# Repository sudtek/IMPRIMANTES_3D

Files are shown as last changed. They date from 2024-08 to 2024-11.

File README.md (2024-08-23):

# IMPRIMANTES_3D

24 août 2024

Ce repository dédié aux imprimantes 3D va regrouper mes howto et tutoriels principalement liés à certaines imprimantes 3D que j'utilise / posséde.
J'utilise principalement des imprimantes 3D pour l'impression de prototypes réalisée sous Catia V5 ,malheureusement par defaut les imprimantes 3D ne sont pas correctement calibrés par les constructeurs.
C'est donc à l'utilisateur de regler son imprimante via des étapes de calibrages pour esperer obtenir une objet 3D précis et fidéles au STL.

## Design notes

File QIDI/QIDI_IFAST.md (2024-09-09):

**24_08_2024**

J'ai recement fait l'acquisition d'une imprimante de marque QIDI modéle IFAST avec une tête dual pour pouvoir imprimer mes piéces du PETG et les supports dans une matiere differente (PLA / PVA) qui n'hadére pas au PETG.
 
 Une imprimante dite "dual" est différent d'une "IDEX" qui posséde deux têtes totalement indépandantes, capables de travailler simultanément, en mirroir en clone...

Les deux extrudeurs de la QIDI IFAST sont montés sur une unique tête et sont alternativement sortis / retractés selon le besoin via une came lorsque la tête arrive en buté gauche / droite. 

Exemple : Si la tête arrive en buté gauche la tête Z2 situé à main gauche est abaissée à proximité du plateau afin de pouvoir imprimmer alors que la tête de droite z1 est elle est retactée.

J'utilise uniquement le sclicer Ideamaker pour convertir mes fichiers STL. Celui-ci identifie les têtes de gauche à droite comme T0,T1 ... ce qui n'est pas sans posser des pb avec la numerotation de QUIDI.

**QUIDI IFAST avec Firmware Marlin modifié par QIDI; certaines fonctions gcodes sont diferentes voir la section [Firmware de la QUIDI IFAST ](https://github.com/sudtek/IMPRIMANTES_3D/tree/235f8ea74b5f1439434741d732e151d05a6209f9/QIDI/IFAST/Firmware)**

| Localisation Extrudeur | Gauche | Droite |
|---|---|---|
| Identification QIDI | Z2 | Z1 |
| Identification Ideamaker| T0 | T1 |
| Localisation | Gauche | Droite |
| Impression | Corps  | Supports |
| Matière à extruder | PETG | PLA |
| Température extrudeurs (°C) | 235 | 205 |
| Température Bed (°C) | 70 | 70 |
| Température enceinte (°C) | 55 | 55 |

- Localisation  : Par convention lorsque l'on fait face à l'imprimante.
- Température extrudeurs (°C) : Par defaut ces températures donneront un bon resultat mais il faudra toujours calibrer vos bobines.
- Température Bed (°C)  : Toujours prevoir un filme de colle blanche pour assurer l'hadérence et limiter le warp et faciliter le retrait par spatulage.
- Température enceinte (°C) : Ne pas dépasser les 55°c sinon les supports / radeaux / jupes en PLA vont fondre et se deformer l'idéal est d'utiliser un pla+ 
- Note 1 : Aucune ventilation de l'impression en cours car cela fait warp le PETG
- Note 2 : A la fin de l'impression il est conseillé de faire via un gcode de baisser la temperature progressivement par palier pour eviter le warping du PETG.

**Mes observation :** Jai rapidement pu consater que les objets imprimés avec ma QIDI IFAST à 1500€ etaient bien moins précis que sur ma vielle X1 300€ calibrée ... La  QIDI Ifast est une imprimante technique qui necesite imperativement une calibration complexe de bout en bout il est impossible de se contenter des réglages par defaut d'usine. J'ai donc decidé de consigner mes périgrinations, methodes, informations, gcode, profils ideamakers et autres galéres ... pour aider les autres utilisateurs qui possédent une QIDI IFAST à tirer le meilleur parti de leur machine. J'ai pris contact avec le support QIDI qui est certes réactif et amical mais qui reste selon moi trop supperficiel sur certains points ... manque de documentation et finition logiciels ... 

**ATTENTION :** Les gcodes de cette catégorie sont trés specifiques aux imprimantex QIDI IFAST !! Vous pouvez vous en inspirer mais si vous avez un autre modele il faudra imperativement les adapter. J'ai pour habitude de documenter mafin que cela soit explicite néanmoins je vous recommande de toujours les relire et verifier avant de vous lancer.

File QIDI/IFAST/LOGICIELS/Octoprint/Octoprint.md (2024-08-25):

**Instructions pour Utiliser OctoPrint avec l'Imprimante Qidi I-Fast**

**Date : 25 août 2024**

Spécifications de l'Imprimante Qidi I-Fast :
- **Modèle** : QIDI TECHNOLOGY I-Fast 3D Printer
- **Extrudeurs** : Double
- **Volume d'Impression** : 360×250×320mm

Ces instructions vous permettront de configurer OctoPrint avec votre imprimante Qidi I-Fast.
Assurez-vous de suivre chaque étape avec précaution hors tension pour éviter tout dommage aux composants internes de l'imprimante.

Pour utiliser le logiciel OctoPrint avec l'imprimante Qidi I-Fast, il est nécessaire d'ajouter un dongle USB vers un port série (VCC; RX; TX; GND), car l'imprimante n'est pas équipée d'origine d'un port USB. Voici les étapes à suivre :

1. **Retirer le Panneau de Droite** :
   - Démontez le panneau de droite de l'imprimante pour accéder aux composants internes.

2. **Localiser le Connecteur Série** :
   - Identifiez le connecteur série à l'intérieur de l'imprimante. Il existe deux ports série, Attention Qidi recommande de connecter le dongle USB au port situé à proximité immédiate du module Wi-Fi.
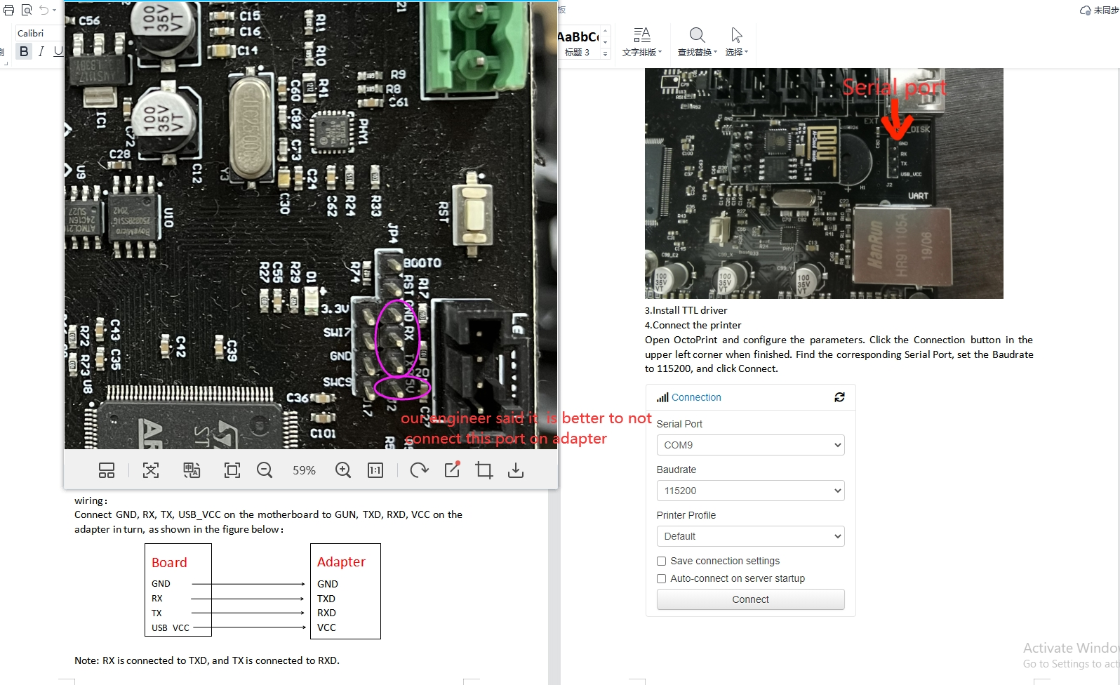
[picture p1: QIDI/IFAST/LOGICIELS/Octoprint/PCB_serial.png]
Le PCB en question est celui visible sur la photo de droite :


3. **Connecter le Dongle USB** :
   - Branchez le dongle USB au connecteur série identifié.
   - Utilisez une rallonge USB pour faciliter la connexion et l'accessibilité.
  
4. **Installer Octoprint** :
   Je ne rentrerai pas dans les details pour vous expliquer comment installer Octoprint ce n'est pas l'objet de ce md; il ya de nombreuses videos qui traitent de ce sujet en profondeur ...  mais  si vous avez plusieurs imprimante 3D je vous recommande d'installer Octoprint en "multi instance" vous pourrez ainsi contrôler plusieurs imprimantes indépandement sans risque d'interferénce et sans avoir besoin d'affecter une machine par imprimante.
   
6. **Note à propos de l'interfacage entre Octoprint et la QIDI IFAST :** Il semble que le firmware de la QIDI IFAST n'est pas totalement pris en charge par Octoprint cela signifie que vous pouvez piloter la QIDI IFAST avec les commandes basiques depuis l'interface web d'Octoprint, exemple : fixer la temperature d'une buse, du beb, bouger la tête, lancer votre impression ... mais certaines fonction propre à l'imprimante seront désactivés et/ou inutilisables voir sans boucle de retour / rétroaction ... Je trouve dommage que QIDI n'accorde pas plus d'interet à un produit comme Octoprint qui unifie les interfaces de controle des imprimantes 3D ... Je pense que c'est une grave erreur commerciale qui coutera très cher à long terme à tous les constructeurs qui ont cette politique de segmentation esperant rendre captif les clients ...

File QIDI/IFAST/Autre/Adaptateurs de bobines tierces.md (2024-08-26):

26_08_2024

Par défaut les bobines de filament tierce se bloquent dans le support de bobine des QIDI ifast car l'axe est étroit c'est problématique, du coup j'ai réalisé un adaptateur les bobines des marques : 

| Marque de Bobine | Din mm | Dout mm |
|---|---|---|
| SUNLU | | |
| noname | | |

Je vous recommande de les imprimer en PETG avec 3 coques et 50% pour une bonne durabilité.

Il vous faudra suprimmer les 4 ergots du couvercle transparent des supports de bobine QUIDI qui maintiennent les bobines centrées car avec cet adapteur cela n'est plus nécesaire.

J'utilise principalement du filamant Sunlu et du noname. Si vous avez reéalisé un adaptateur de bobine pour la QIDI IFAST et que vous soulez uploader ici vous êtes le bienvenu

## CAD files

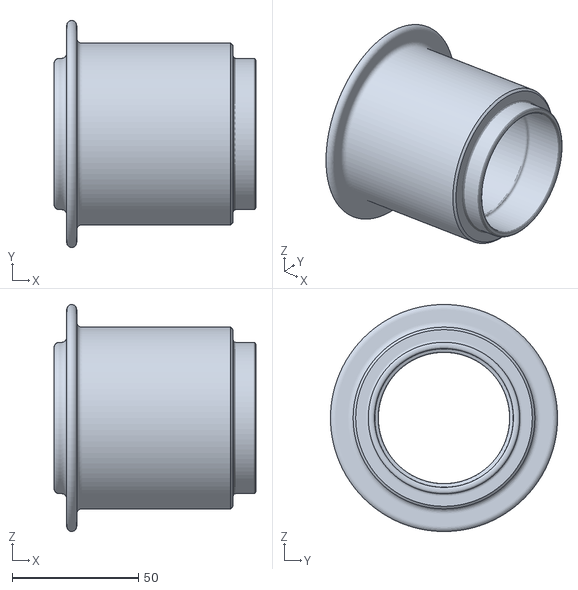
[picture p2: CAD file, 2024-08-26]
QIDI/IFAST/Autre/Adaptateur de bobine Sunlu pour QIDI IFAST/STL/adaptateurBobineSunluPourIFAST_corps.stl
80.0 x 90.0 x 90.0

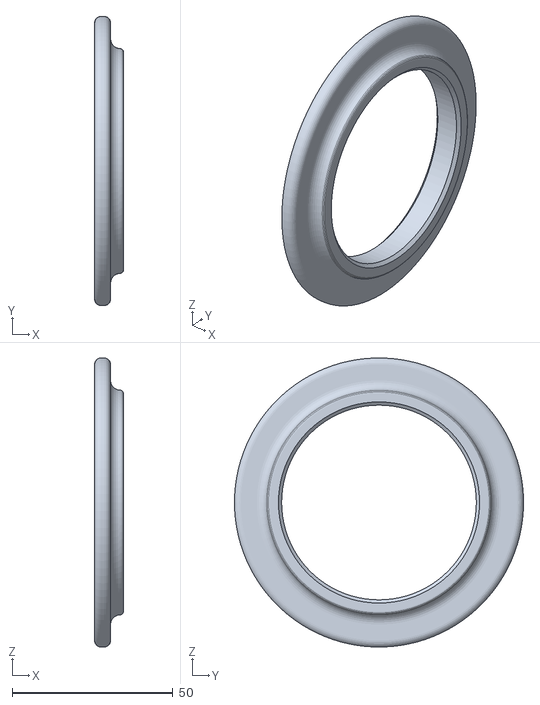
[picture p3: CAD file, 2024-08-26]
QIDI/IFAST/Autre/Adaptateur de bobine Sunlu pour QIDI IFAST/STL/adaptateurBobineSunluPourIFAST_Anneau.stl
9.00 x 90.0 x 90.0

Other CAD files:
QIDI/IFAST/Autre/Adaptateur de bobine Sunlu pour QIDI IFAST/CATIA V5/adaptateurBobineSunluPourIFAST.CATPart

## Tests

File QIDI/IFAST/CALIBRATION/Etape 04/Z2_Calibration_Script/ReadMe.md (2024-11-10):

**05/11/2024**

**Génerateur de séries de cubes à débit variable par pas décroissants constants de 1% / 0.1% pour calibration et encadrement du débit de Z2 (buse de gauche) sur imprimante 3D QIDI-IFAST.**

Aprés avoir réalisé la vidéo [E01 de l'étape 04 du tutoriel de calibration pour trouver le débit % d'un filament sur Z2 QIDI-IFAST](https://youtu.be/gn3A1lFX0vc) explicative pour approfondir [Etape 04 caractériser le % débit d'un nouveau filament](https://github.com/sudtek/IMPRIMANTES_3D/tree/f0b85f540401e21b22918730633c640832fa8458/QIDI/IFAST/CALIBRATION/Etape%2004) j'ai pris conscience que devoir systématiquement modifier manuellemment dans IDEAMAKER les débits de 11 cubes c'est long, fastidieux, sujet à erreur ... deplus les étiquettes de débit des cubes ex : 100% ; 99% ... devaient être mofifiées pour chaque nouvelle série de débit de cubes / pas afin de garder un minimum de cohérence.  Devant ce constat je me suis lancé dans l'écriture d'un script python nommé **Z2_generate.py** qui génére automatiquement un gcode de calibration des cubes éprouvettes en posant 16 questions à l'utilisateur pour générer 11 cubes étiquettés de A (cube avec le débit maximum situé le plus à gauche) à K (cube avec le débit minimum situé le plus à droite). Plus besoins d'éditer le fichier source .IDEA via IDEAMAKER et modifier manuellemment les débits d'écoulements, etiquettes ... Attention à ce jour (05/11/2024) ce script fonctionne uniquement pour la buze de gauche Z2 une variante pour calibrer Z1 devrait être réalisé ...

[/.](https://github.com/sudtek/IMPRIMANTES_3D/tree/7fcbe4567642c7eb1b9e53f8b73f05a81d9aab80/QIDI/IFAST/CALIBRATION/Etape%2004/Z2_Calibration_Script) :

- [ReadMe.md](https://github.com/sudtek/IMPRIMANTES_3D/blob/7cafb12449ad44995997dd2e7e61ac8081cbc6da/QIDI/IFAST/CALIBRATION/Etape%2004/Z2_Calibration_Script/ReadMe.md) : Ce fichier explicatif.
  
- [Z2_generate.py](https://github.com/sudtek/IMPRIMANTES_3D/blob/b0ba36f662e1e2850cdf81203b2ab84ad15976f0/QIDI/IFAST/CALIBRATION/Etape%2004/Z2_Calibration_Script/Z2_generate.py) : Permet de générer un fichier gcode de sortie sous une forme explicite et compréhensible exemple : [01_11_2024_Z2_Calibration_[100.0%..90.0%]_Pas_-1.0%_PETG_Blanc_SUNLU_235°c_1.724mm.gcode](https://github.com/sudtek/IMPRIMANTES_3D/blob/7fcbe4567642c7eb1b9e53f8b73f05a81d9aab80/QIDI/IFAST/CALIBRATION/Etape%2004/Z2_Calibration_Script/Exemples/01_11_2024_Z2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). Ce script écrit en python V3.0 est simple et ne requier aucun argument. Il ne doit pas être édité hormis si vous désirez modifier des valeurs par defaut de certaines variables.
  
- [26_10_2024_Z2_Calibration_[X%..Y%]_Pas_N%_TEMPLATE_01.gcode](https://github.com/sudtek/IMPRIMANTES_3D/blob/b0ba36f662e1e2850cdf81203b2ab84ad15976f0/QIDI/IFAST/CALIBRATION/Etape%2004/Z2_Calibration_Script/26_10_2024_Z2_Calibrat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)  : est le fichier template qu'utilise "[Z2_generate.py](https://github.com/sudtek/IMPRIMANTES_3D/blob/b0ba36f662e1e2850cdf81203b2ab84ad15976f0/QIDI/IFAST/CALIBRATION/Etape%2004/Z2_Calibration_Script/Z2_generate.py)" pour rechercher et insérer des blocs de gcodes suites aux interactions avec l'utilisateur. Il doit imperativement être en lecture seule au besoin modifier ses attributs car il et ne doit pas être edité. **Ce fichier doit impérativement être dans le même repertoire que Z2_generate.py**. Ce fichier ne doit pas être lu avec un slicer car il contient des blocs de textes; il peut être ouvert avec un simple éditeur de texte.

[/Source](https://github.com/sudtek/IMPRIMANTES_3D/tree/7fcbe4567642c7eb1b9e53f8b73f05a81d9aab80/QIDI/IFAST/CALIBRATION/Etape%2004/Z2_Calibration_Script/SOURCE) :
- [ORI 25_10_2024_Calibration_[X%..Y%]_Pas_N%.gcode](https://github.com/sudtek/IMPRIMANTES_3D/blob/7fcbe4567642c7eb1b9e53f8b73f05a81d9aab80/QIDI/IFAST/CALIBRATION/Etape%2004/Z2_Calibration_Script/SOURCE/ORI%2025_10_202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) : Le fichier gcode original sliccé généré par IDEAMAKER. Il est imprimable et fonctionel mais ce fichier est particulier; il est fourni pour mémoire car il m'a permis d'identifier et différentier les blocs de gcodes pour fabriquer le template. En effet ce gcode fait plus de 80OOO lignes j'ai donné des valeurs de débit volontairements particuliéres et uniques à chacun des élements afin de pouvoir les distinguer des les uns des autres. J'ai fait en sorte qu'aucun élements que j'ai créé n'est la valeur de débit = 100% ainsi j'ai pu identifier et trouver chacun des élements. Exemple :

Le cube A débit -> 101%, cube B débit -> 99 % ... decroisant de -1% ... cube K débit -> 90 %.

La tour de purge -> 105%.

La légende de A à K -> 103%.

- [Z2_recalibration.txt](https://github.com/sudtek/IMPRIMANTES_3D/blob/7fcbe4567642c7eb1b9e53f8b73f05a81d9aab80/QIDI/IFAST/CALIBRATION/Etape%2004/Z2_Calibration_Script/SOURCE/Z2_recalibratio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) : Fichier texte récapitulatif qui identifie tous les blocs BLOC_XXXXX_XXXXX , le nb d'occurences, le gcode à modifier  ... dans "ORI 25_10_2024_Calibration_[X%..Y%]_Pas_N%.gcode" pour en faire un template.

- [05_11_2024_IDEAMAKER_Calibration.zip](https://github.com/sudtek/IMPRIMANTES_3D/blob/25a1928895052bc615755bc975bd8cc815079d67/QIDI/IFAST/CALIBRATION/Etape%2004/Z2_Calibration_Script/SOURCE/05_11_2024_IDEA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) : Ce Zip contient tous les fichiers sources pour IDEAMAKER V5.0.6.8380 (ou supérieur) pour (ré)générer le gcode de départ cela inclus également tous mes profils (profil imprimante IFAST-QIDI, 2 profils filaments PETG & PLA, profils paramètres & groupes, profils.bin), les fichiers .STL pour la legende de A à K, le fichier code ci-dessus et le fichier 24_10_202_Calibration_[X%..Y%]_Pas_N%.idea qui au besoin vous permettront de générer n'importe quelle série manuellement via IDEAMAKER.

[/Exemples :
](https://github.com/sudtek/IMPRIMANTES_3D/tree/204e1972eb45fdd40d08dab5522a269e7cdda403/QIDI/IFAST/CALIBRATION/Etape%2004/Z2_Calibration_Script/Exemples) :

[01_11_2024_Z2_Calibration_[100.0%..90.0%]_Pas_-1.0%_PETG_Blanc_SUNLU_235°c_1.724mm.gcode](https://github.com/sudtek/IMPRIMANTES_3D/blob/7fcbe4567642c7eb1b9e53f8b73f05a81d9aab80/QIDI/IFAST/CALIBRATION/Etape%2004/Z2_Calibration_Script/Exemples/01_11_2024_Z2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)

[01_11_2024_Z2_Calibration_[92.0%..91.0%]_Pas_-0.1%_PETG_Blanc_SUNLU_235°c_1.724mm](https://github.com/sudtek/IMPRIMANTES_3D/blob/7fcbe4567642c7eb1b9e53f8b73f05a81d9aab80/QIDI/IFAST/CALIBRATION/Etape%2004/Z2_Calibration_Script/Exemples/01_11_2024_Z2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).

Si vous desirez tester un gcode de calibration généré pour la IFAST-QIDI vous pouvez télécharger un des deux fichiers ci-dessus mais *Attention* ils ont été généré pour imprimer avec du PETG sur Z2 (et du PLA sur Z1) si vous êtes dans cette configuration vous pouvez les lancer direct sur votre IFAST mais si ce n'est pas le cas il vous faudra générer votre propre série en invoquant [Z2_generate.py](https://github.com/sudtek/IMPRIMANTES_3D/blob/b0ba36f662e1e2850cdf81203b2ab84ad15976f0/QIDI/IFAST/CALIBRATION/Etape%2004/Z2_Calibration_Script/Z2_generate.py). Je placerai mes nouvelles séries (les plus courantes) au fur et à mesure dans ce répertoire ainsi vous pourrez en profiter mais il vous faudra toujours penser à remplacer la valeur **Filament Diameter #2** par celle de votre filament [Etape 03 : Calibration du diamètre du filament](https://github.com/sudtek/IMPRIMANTES_3D/blob/main/QIDI/IFAST/CALIBRATION/Etape%2003/Etape_03.md) :

```
;_DEBUT_[informations des filaments]
...
;Note : Modifier cette valeur avec le diamètre de VOTRE FILAMENT est impératif pour trouver votre débit ! 
;Filament Diameter #2: 1.724
...
;_FIN_[informations des filaments]
```

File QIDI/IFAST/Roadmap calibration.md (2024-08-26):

Ce qu'il va falloir faire ....

<s>
;//FAIT
; A faire Fixer avant la temperature de la buse et attendre X minutes
; exemple : ideal extruding length is 100mm,but actually it flew out 93mm.
; So the correct e step should be 93*0.0073/100,it is 0.006789
;//FAIT
</s>
;
;Bloc 1 : Pour régler indépendamment les paramètres des moteurs pas-à-pas XY, utilisez cette commande (cochez la case dans le cadre ci-dessus).
M8009 X0.010625 Y0.010625

;Bloc 2 : La valeur en mm de chaque pas est calculée à l'aide de la formule suivante : pas (360/18)*16. Le pas est la distance que la plate-forme monte lorsque la vis tourne d'un tour.
M8010 S0.0025

**
;
;Bloc 3 : La valeur en mm de chaque pas est égale à la circonférence de la roue d'entraînement d'extrusion divisée par 3200.
;         Si vous avez un dispositif de réduction, divisez également par le rapport de réduction. Si vous constatez que le filament est extrudé de manière trop lâche, ou... 
          Une nouvelle suggestion est de rendre cette valeur légèrement inférieure à la valeur réelle, l'extrusion sera meilleure.
;M8011 S0.0073 P0.0073
;M8011 S0.0067 P0.0067
;**

;Bloc 4 : Vitesse maximale pour les mouvements XY en mm/s. Afin d'assurer la stabilité de la machine, veuillez régler cette valeur en fonction des résultats de vos tests.
M8012 1200

Bloc 5 : Vitesse maximale pour les mouvements Z en mm/s.
M8013 110

;Bloc 6 : Vitesse maximale de l'extrudeur en mm/s.
M8014 1120
 
;Bloc 7 : La première vitesse de homing de l'axe Z. La vitesse est relativement rapide. Le logiciel de découpage MakerWare ignorera cette vitesse de homing car le G-code qu'il génère spécifie une vitesse de homing.
Explications supplémentaires (basées sur les commentaires)
* Paramètres des moteurs pas-à-pas: Les commandes M8009 et M8010 permettent de régler la précision des mouvements des axes X et Y en fonction des caractéristiques des moteurs et de la vis mère.
* Calcul du pas: Le commentaire explique comment calculer le pas de l'axe Z en fonction du pas de la vis mère. Cette valeur est essentielle pour une extrusion précise du filament.
* Vitesse d'extrusion: La commande M8011 et le commentaire associé concernent la vitesse maximale à laquelle le filament peut être extrudé. Une valeur trop élevée peut entraîner des problèmes d'adhérence ou de sous-extrusion.
* Vitesses maximales: Les commandes M8012, M8013 et M8014 définissent les vitesses maximales pour les mouvements des axes X, Y et Z, ainsi que pour l'extrusion. Ces valeurs doivent être ajustées en fonction des capacités de la machine et du matériau utilisé.
* Homing de l'axe Z: Le dernier commentaire mentionne que la vitesse de homing de l'axe Z peut être ignorée par certains logiciels de découpage, car ils spécifient leur propre vitesse dans le G-code généré.

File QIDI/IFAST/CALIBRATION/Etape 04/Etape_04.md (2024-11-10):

# Étape 04 : Détermination du débit % en fonction du diamètre du filament

## Prérequis avant de continuer
Vous devez impérativement avoir effectué les étapes suivantes pour la QIDI IFAST : 
- [Etape 00 : Réglage de l'alignement des deux buses / calibrage XY](https://github.com/sudtek/IMPRIMANTES_3D/blob/main/QIDI/IFAST/CALIBRATION/Etape%2000/Etape_00.md)
- [Etape 01 : Calibration des deux moteurs d'extrusion de Z1 / Z2](https://github.com/sudtek/IMPRIMANTES_3D/blob/main/QIDI/IFAST/CALIBRATION/Etape%2001/Etape_01.md)
- [Etape 03 : Calibration du diamètre du filament](https://github.com/sudtek/IMPRIMANTES_3D/blob/main/QIDI/IFAST/CALIBRATION/Etape%2003/Etape_03.md)

_Note 05/10/2024 : Une nouvelle solution de Détermination du débit % ne nécessite plus l'utilisation d'IDEAMAKER. Un script Python est employé pour générer un fichier Gcode personnalisé, permettant de caractériser les filaments sur la buse Z2._

## Présentation
Ce tutoriel détaille étape par étape la méthode pour déterminer et encadrer le pourcentage de débit optimal d'un filament afin d'obtenir des impressions avec une précision dimensionnelle accrue. Le processus comprend tous les fichier source pour génèrer des cubes éprouvettes à des débits variables, la mesure précise des parois des cubes et l'analyse des données pour déterminer le débit optimal d'un filament donné.

Exemple pour le logiciel sliccer IDEAMAKER : 

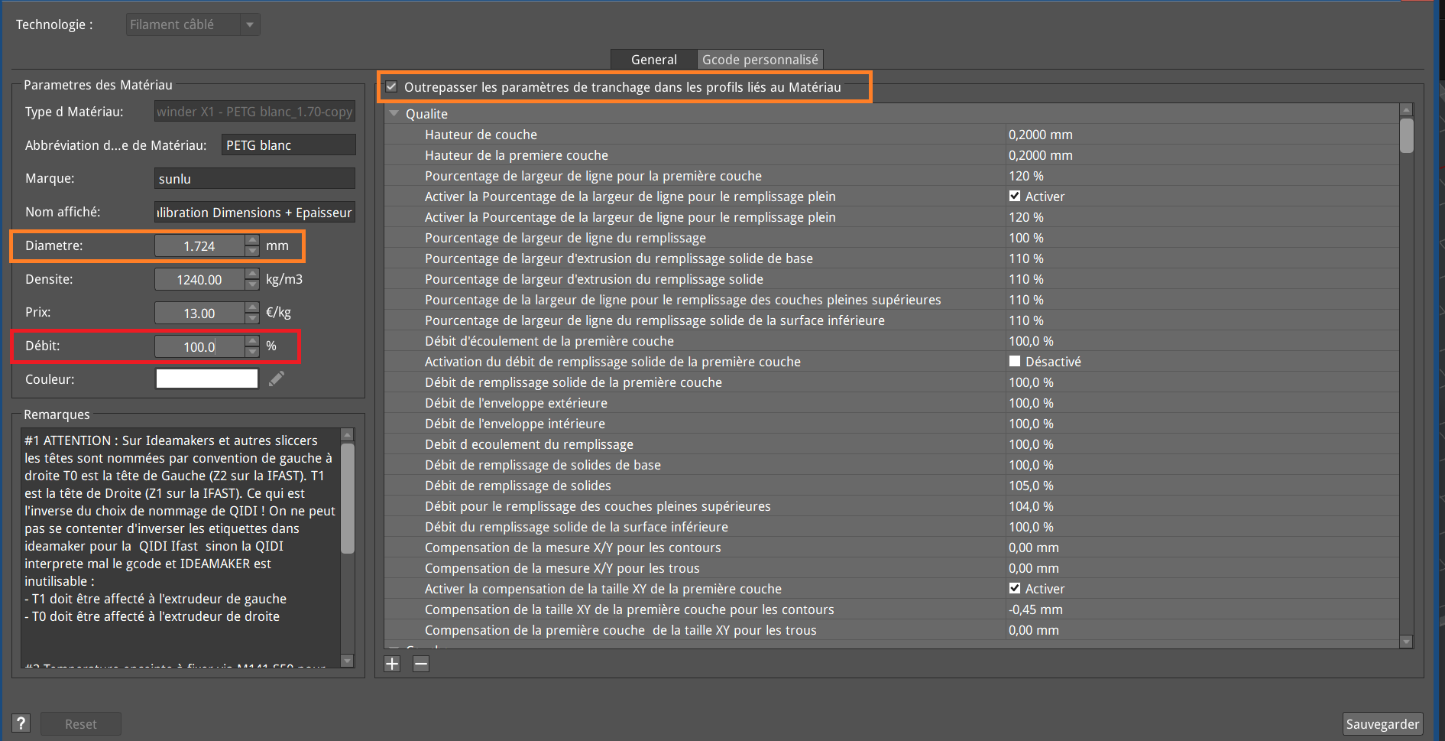
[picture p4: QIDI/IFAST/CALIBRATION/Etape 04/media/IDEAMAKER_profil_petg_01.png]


Pour déterminer la valeur exacte du pourcentage de débit propre à un filament donné (encadrée en rouge) il est impératif que le diamètre du filament (par exemple, 1,724 mm, encadré en orange) ait été défini avant de poursuivre ce tutoriel. En cas de non-définition, veuillez vous reporter à[Etape 03 : Calibration du diamètre du filament](https://github.com/sudtek/IMPRIMANTES_3D/blob/main/QIDI/IFAST/CALIBRATION/Etape%2003/Etape_03.md)

_Note : Toutes les méthodes mises en œuvre dans ce tutoriel consistent à imprimer les éléments du plateau couche par couche, sans recourir à l'impression séquentielle. Cette approche est nécessaire car l'impression séquentielle ne permet pas d'imprimer 11 cubes côte à côte avec une distance intercubes de 5 mm sans risquer de collisions.._ 

## Objectif
L'objectif principal de ce tutoriel est d'expliquer étape par étape, comment le débit en pourcentage d'un filament PETG SUNLU est caractérisé sur la buse Z2 (buse gauche) d'une QIDI-IFAST, en utilisant une série de cubes de test à des débits variables décroissants. Le but est de trouver la valeur optimale de débit en pourcentage qui permet d'obtenir des parois de cube avec une épaisseur la plus proche possible de la valeur théorique de 1,6 mm (0,4 mm x 4). Quel que soit le slicer utilisé (IDEAMAKER dans mon cas), il est toujours nécessaire de définir cette valeur avec précision (ainsi que le diamètre nominal) pour tirer le meilleur de votre imprimante. Chaque filament est unique et doit être caractérisé avant utilisation. Par expérience, je vous conseille de noter ces deux valeurs sur la bobine, ce qui vous facilitera grandement la tâche.

# Étape 04 : Calibration du pourcentage de débit d'écoulement de la buse Z1/Z2 en fonction du diamètre du filament

## Méthodologie de principe : Étapes du Processus avec les cubes de [100% .. 90%] par pas de 1%

**Chargement de Fichiers**
   
   **Cas 1** : Vous avez la même configuration que moi sur votre QIDI-IFAST du PETG sur Z2 et du PLA sur Z1 -> vous pouvez lancer l'[Impression des Cubes](https://github.com/sudtek/IMPRIMANTES_3D/edit/main/QIDI/IFAST/CALIBRATION/Etape%2004/Etape_04.md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) de la série de 11 cubes du fichier [17_10_2024_Calibration_[100%..90%]_V2.gcode](https://github.com/sudtek/IMPRIMANTES_3D/blob/7b1b4db4feb8aaa148066c3f2ab6458e4ebc0bf5/QIDI/IFAST/CALIBRATION/Etape%2004/Z2_Calibration_PETG_235%C2%B0c/17_10_2024_Ca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).
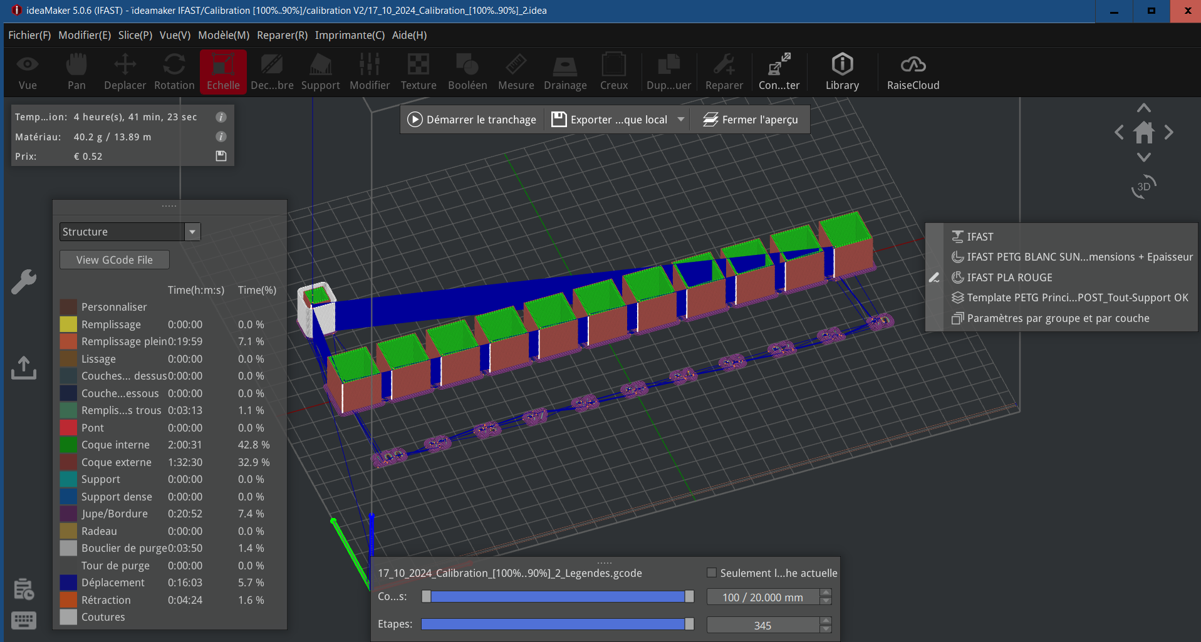
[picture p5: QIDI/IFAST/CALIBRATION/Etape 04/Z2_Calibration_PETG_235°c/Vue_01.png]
   

   **Cas 2 :** Vous n'avez pas la même configuration que moi et/ou vous désirez (éditer / modifier / adapter) le fichier sources [17_10_2024_Calibration_[100%..90%]_V2.idea](https://github.com/sudtek/IMPRIMANTES_3D/blob/b954e0fb5198141b21f86ee10baec49635fdae2a/QIDI/IFAST/CALIBRATION/Etape%2004/Z2_Calibration_PETG_235%C2%B0c/17_10_2024_Ca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) à vos besoins, tous les fichiers peuvent être téléchargés sur ce lien [Etape 04
/Z2_Calibration_PETG_235°c](https://github.com/sudtek/IMPRIMANTES_3D/tree/7b1b4db4feb8aaa148066c3f2ab6458e4ebc0bf5/QIDI/IFAST/CALIBRATION/Etape%2004/Z2_Calibration_PETG_235%C2%B0c)

  - Lancer le logiciel IDEAMAKER (Version >= 5.0.6).
    
  - Charger le fichier [17_10_2024_Calibration_[100%..90%]_V2.idea](https://github.com/sudtek/IMPRIMANTES_3D/blob/b954e0fb5198141b21f86ee10baec49635fdae2a/QIDI/IFAST/CALIBRATION/Etape%2004/Z2_Calibration_PETG_235%C2%B0c/17_10_2024_Ca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)
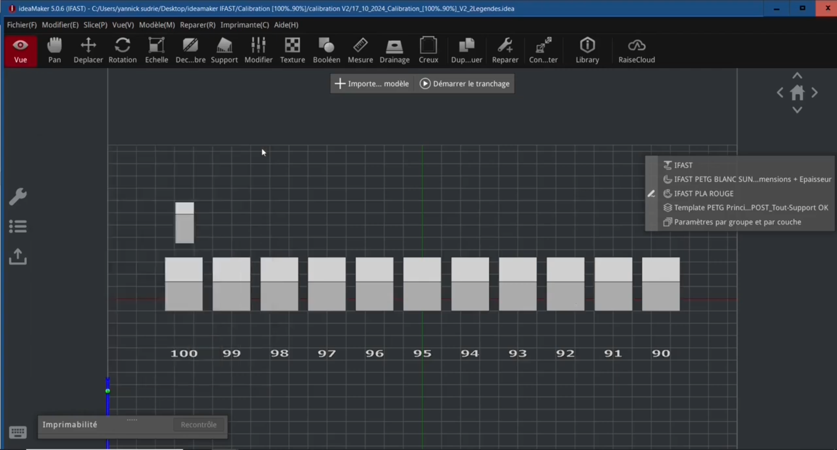
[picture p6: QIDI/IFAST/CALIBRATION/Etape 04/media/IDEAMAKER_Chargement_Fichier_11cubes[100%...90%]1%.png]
    
    
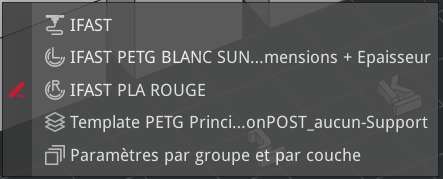
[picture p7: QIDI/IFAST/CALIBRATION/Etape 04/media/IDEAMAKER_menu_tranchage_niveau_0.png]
 - Depuis le menu de tranchage simplifié appuyer sur l'icone stilo rouge 

   pour acceder au menu de tranchage detaillé qui devrait être vierge :
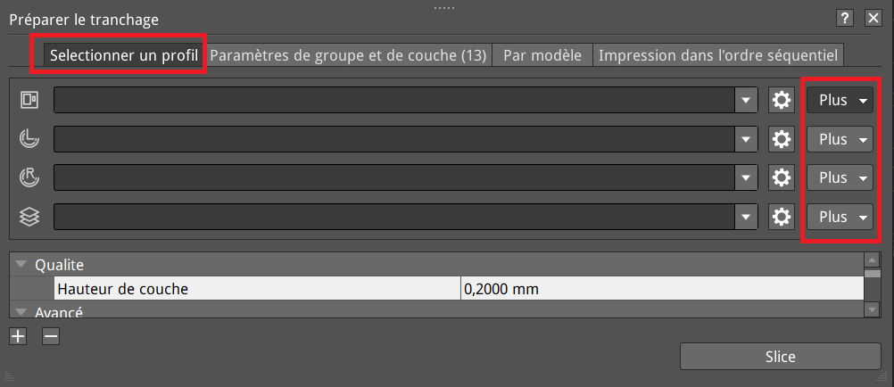
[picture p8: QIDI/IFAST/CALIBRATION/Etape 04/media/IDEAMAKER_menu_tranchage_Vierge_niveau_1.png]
   
   
 - Importer de haut en bas les profils liés à l'imprimante QIDI-IFAST, du filament de gauche et celui de droite, du template ... via les boutons "Plus"
   
 De haut en bas :

 #1 Importer le profil de l'imprimante 
 [17_10_2024_IFAST-export.printer](https://github.com/sudtek/IMPRIMANTES_3D/blob/667637b22536c230eb82010f8e05996019708a51/QIDI/IFAST/CALIBRATION/Etape%2004/Z2_Calibration_PETG_235%C2%B0c/17_10_2024_IF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)
dans la 1er ligne en appuyant sur Plus :
 

 #2 Importer le profil du matériaux sur la buse Z2 située à gauche (L) pour LEFT (en)
 [17_10_2024_QIDI_IFAT_PETG blanc_export_Gauche.filament](https://github.com/sudtek/IMPRIMANTES_3D/blob/4566f302fe43216aef2d1f766e220cac8bce1b17/QIDI/IFAST/CALIBRATION/Etape%2004/Z2_Calibration_PETG_235%C2%B0c/17_10_2024_QI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)
dans la seconde ligne en appuyant sur Plus :
 

 #3 Importer le profil du matériaux sur la buse Z1 située à droite (R) pour RIGHT (en)
 [17_10_2024_QIDI_IFAT_PLA_Rouge_export_Droite.filament](https://github.com/sudtek/IMPRIMANTES_3D/blob/3f0e0337d4df9fc1193c668eef40fb1c53a33e74/QIDI/IFAST/CALIBRATION/Etape%2004/Z2_Calibration_PETG_235%C2%B0c/17_10_2024_QI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)
dans la troisième ligne en appuyant sur Plus :


 #4 Importer le profil du template* matériaux
 [Etape 04/Z2_Calibration_PETG_235°c/17_10_2024_Template PETG Principal GAUCHE_QIDI_Z2T0 VS PLA supports DROITE_QIDI_Z1_T1 SAVE_17_octobre_2024_nonPOST_Tout-Support_OK_export.bin](https://github.com/sudtek/IMPRIMANTES_3D/tree/4566f302fe43216aef2d1f766e220cac8bce1b17/QIDI/IFAST/CALIBRATION/Etape%2004/Z2_Calibration_PETG_235%C2%B0c)
dans la seconde ligne en appuyant sur Plus :
 
 
_*(Note : ATTENTION risque de confusion : Dans le tutoriel utilisant le script utilise aussi le terme template mais ils n'ont rien en commun !)_

Vous devriez avoir cette présentation : 
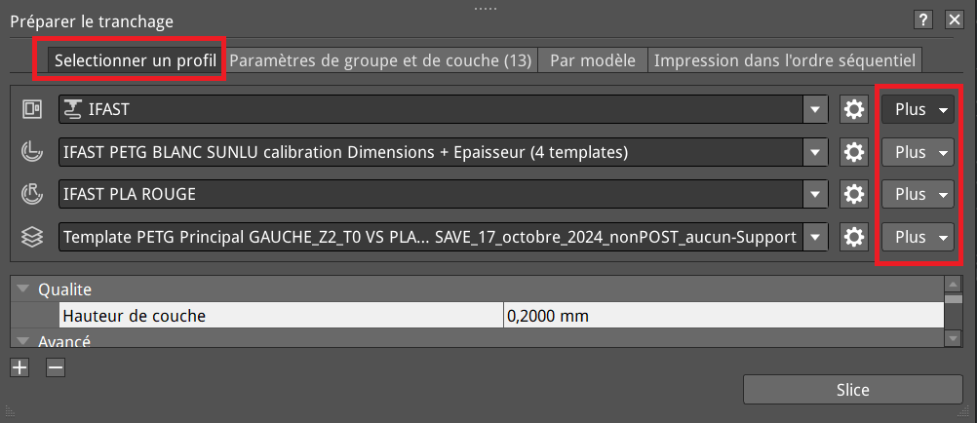
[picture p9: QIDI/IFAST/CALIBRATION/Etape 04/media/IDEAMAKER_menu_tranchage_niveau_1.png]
 

Importer le fichier paramétrage des 11 cubes "**Paramètres de groupes et couches**" -> "**Importer et Exporter**" -> "**Importer d'un disque Local**" 
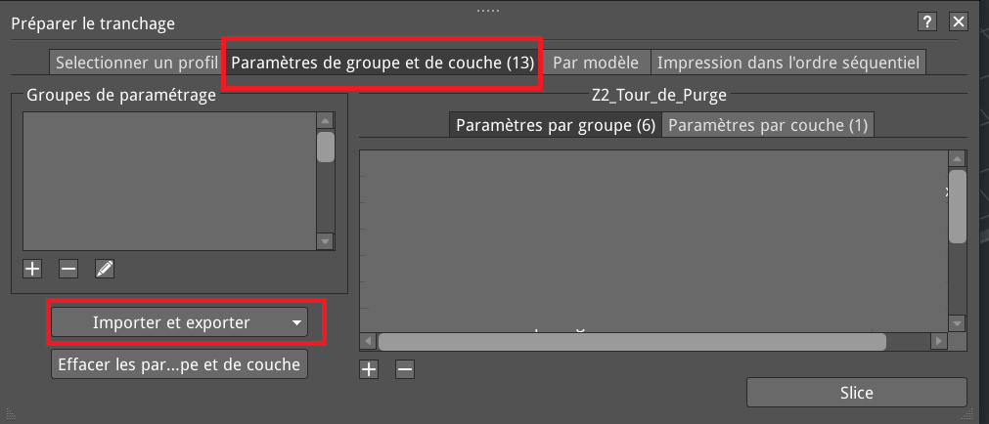
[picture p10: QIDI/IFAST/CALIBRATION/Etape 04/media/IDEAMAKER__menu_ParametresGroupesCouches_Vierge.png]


Choisir le fichier [17_10_2024_Calibration_[100%..90%]_V2_export.settinggroup](https://github.com/sudtek/IMPRIMANTES_3D/blob/7cd00734a7899714554ef4374b111f3f644160e2/QIDI/IFAST/CALIBRATION/Etape%2004/Z2_Calibration_PETG_235%C2%B0c/17_10_2024_Ca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). Ce fichier contient toutes les paramètres qui **SURPASSENT (ECRASENT)** les paramètres du profil matériaux PETG sur Z2 afin de créeer des groupes possédant chacun un pourcentage de débit propre / unique qui ne dépend plus du profil du matériaux sur la buse Z2 située à gauche. Ainsi dans IDEAMAKER chaque élement du plateau peut être customisé et avoir ses propres spécifités par groupe et / ou couche. 

_Note : Les fichiers avec l'extension "**.settinggroup**" n'ont en général de sens qu'avec le fichier le fichier "**.idea**" auquel ils sont associés et par nature ne sont que "peut" transposables / associables à d'autres items hormis pour récupérer des configurations particulières.
_

Si l'import des paramètres c'est bien déroulé vous devriez voir une liste de groupes correspondats aux éléments des 11 Cubes, de la légende et de la tour de purge :
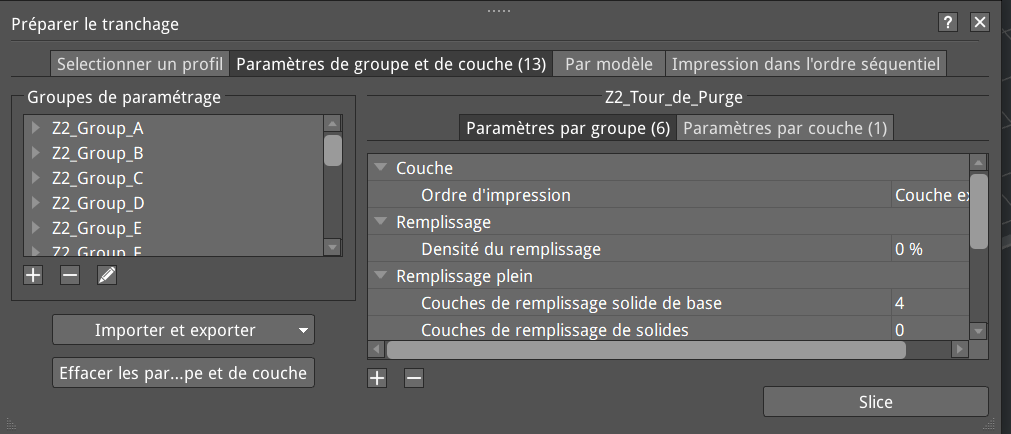
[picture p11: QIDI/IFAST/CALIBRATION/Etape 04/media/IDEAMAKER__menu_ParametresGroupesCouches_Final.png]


Exemple : Détails des paramètres propres et uniques à chaque groupe, ici le groupe B : 
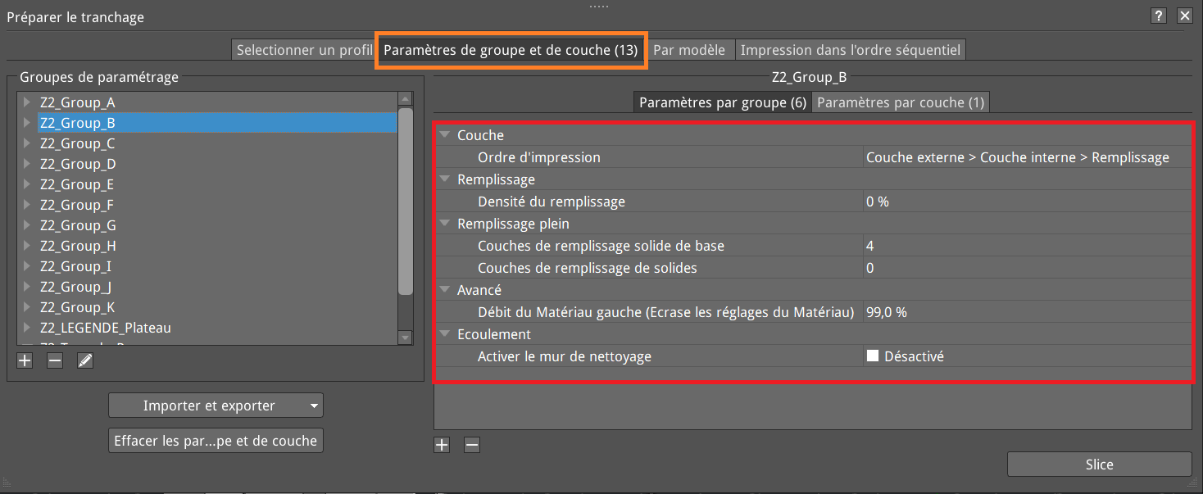
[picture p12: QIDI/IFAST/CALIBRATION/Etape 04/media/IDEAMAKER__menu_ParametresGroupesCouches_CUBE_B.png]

 
Paramètres customisés du Cube débit 99.0% :

**Ordre d'impression*** : N'est pas le même que les autres objets du plateau; le cube du groupe B à ses parois imprimés dans un ordre précis #1 la parois / coque périphérie externe, #2 la parois / coque coque périphérie interne et finalement #3 le remplissage entre les deux coques, ce choix assure un positionement plus précis et une précision de l'épaisseur finale des parois en limitant les effets liés à des poussés latérales.
_Note : Attention le terme Ordre d'impression dans cette option n'a rien avoir avec la possibilité d'impression séquentiel qui consiste elle à imprimer intégralement un cube de la première couche z=0mm à la derniere couche z=20mm avant de passer au prochain cube.
_
**Densité du remplissage** : Ne concerne que l'intérieur du cube, ce paramètre est fixé à 0% afin que notre cube soit vide pour pouvoir mesurer les parois au  1/100 avec un micromètre.

**Couche de remplissage solide** : C'est le nombre de couches en contact avec le plateau / bed. On aurait pu se contenter de la valeur par défaut contenu dans le profil du matériaux PETG (Z2) mais je désirais avoir un nombre de coques uniforme sur toutes l'éprouvette pour limiter les déformations des éprouvettes mais également pouvoir les recyler en récipients ...  

**Débit du matériaux gauche (Ecrase les réglages du materiaux)** : Chaque cube a un débit customisé unique qui est propre à son groupe, le cube du groupe B est imprimé à 99%; le cube suivant du groupe C est imprimé à 98%, etc ... écrasant les réglages des matériaux.

**Activer le mur de netoyage** : Inclus mais désactivé, par défaut cette option est toujours activée dans mon "profil du matériaux" pour le PETG car j'imprime avec deux filaments, mais dans le cadre de la calibration afin de pouvoir imprimer les cubes sur une seule et unique ligne j'ai choisi de désactiver cette option au niveau des groupes cela a pour avantages de ne pas avoir à (re)modifier mon profil matériaux, éviter des colisions entre murs de netoyages étant donné que la distance intercubes est de 5mm mais également accélérer l'impression du plateau. La tour de purge 10x10x20mm elle n'integre pas cette option et donc posséde un mur de netoyage.

Les **Paramètres de couches** : Egalement customisés avec des options qui concernent uniquement la témpérature des extrudeurs dans le but de faciliter la réutilisation et modification de ce plateau pour caracteriser d'autres types de filaments nécèssitant d'autres températures, il faut donc modifier ces valeurs dans chacun des groupes et faire impérativement une verification des valeurs thermiques appliqués à la buse avant d'exporter et imprimer un gcode. Mes vaparamêtres :
Buse Z2 située à gauche (L) 235°c pour le PETG
Buse Z1 située à droite (R) 205°c pour le PLA -> Attention même si ce plateau imprime du PETG la QIDI-IFAST au départ de chaque impression la QIDI-IFAST fait un trait de purge de 100mm de longueur, si la température de Z1 n'est pas adéquate avec la température du filament que vous avez chargé il y a un risque de casser / endomager la tête et/ou boucher la buse. 

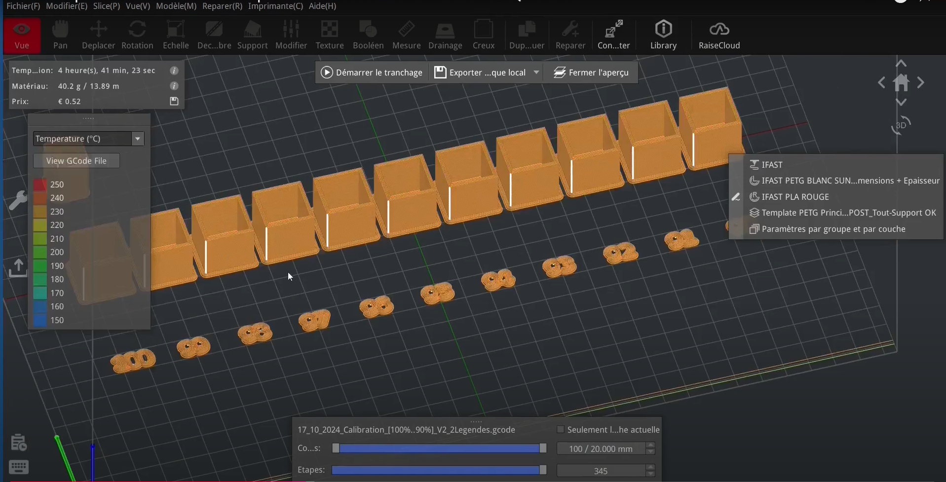
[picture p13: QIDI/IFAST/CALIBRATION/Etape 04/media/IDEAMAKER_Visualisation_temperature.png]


 La température de l'enceinte est fixé par defaut à 40°c, elle peut être modifiée dasn IDEAMAKER en éditant le matériaux principal sur Z2 -> "**IFAST PETG BLANC SUNLU**" -> "**Modifier les paramètres du Matériaux selectionné**" -> "**Gcode Personalisé**" et modifiant le gcode "**M141 S40**". Le choix de cette température n'est pas anodine cela  permet à la fois d'imprimer n'importe quel type de filament tout en ayant une dilation totalement controlée de l'imprimante. En effet etant donné que ma QIDI est localisée dans un atelier elle subit une amplitude thermique d'environ 35°c entre la saison hivernale et estivale; ainsi travailler dans une enceinte à température constante et contrôlée assure une meilleure répétatiblité d'impression et une constance des réglages indépendement de la saison, les mécanismes d'entrainements sont sensibles aux dilations d'ou l'idée de travailler toujours à température constante de 40°.

La température du plateau est fixée à 65°c car j'imprime en PETG le corps de piéce et mes supports en PLA [sur une fine couche de colle soluble](https://github.com/sudtek/IMPRIMANTES_3D/blob/main/QIDI/IFAST/CALIBRATION/Etape%2002/Etape_02.md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), il faut donc trouver une temperature medianne qui est compatible avec les deux filaments.


Rendu de la serie de cubes de calibrage de 100% à 90% à débits dècroissants par pas de 1.0% afin de s'assurer que tout est correct.

Faites un export du fichier .gcode [17_10_2024_Calibration_[100%..90%]_V2.gcode](https://github.com/sudtek/IMPRIMANTES_3D/blob/8bae97a4e72fbc0f8e1de0a924a69d353455d964/QIDI/IFAST/CALIBRATION/Etape%2004/Z2_Calibration_PETG_235%C2%B0c/17_10_2024_Ca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) vers une clef USB.

### Préparation de l'imprimante avant d'imprimer le gcode
Fixer manuellement les températures des materiaux, du plateau et de l'enceinte via le menu de l'imprimante et laisser l'imprimante se dilater et stabiliser au moins 15 minutes avant de lancer votre impression. Je vous invite à vous reporter aux explications détaillés sur ce point l'[Etape 2 Calibration Mise à niveau / hauteur du plateau](https://github.com/sudtek/IMPRIMANTES_3D/blob/main/QIDI/IFAST/CALIBRATION/Etape%2002/Etape_02.md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)

Faites un fast Leveling à chaud de l'imprimante au besoin se reporter à [Étape 02 : Calibration Mise à niveau / hauteur du plateau](https://github.com/sudtek/IMPRIMANTES_3D/blob/8bae97a4e72fbc0f8e1de0a924a69d353455d964/QIDI/IFAST/CALIBRATION/Etape%2002/Etape_02.md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)

### Impression des Cubes
L'impression va durer environ 4 heures 1/4 et consommer 37g de filament.

Chaque couche de cube est imprimée avec un débit d'écoulement unique décroissant 100.0%; 99.0% ... 90.0% mais la QIDI-IFAST a un bug* d'affichage ... L'écran de l'imprimante QIDI-IFAST n'est jamais mis à jour avec la valeur du débit courant et il faut forcer manuelement le rafraichissement de cette valeur en basculant entre l'écran 1/2 et 2/2 pour verifier que les bon paramètres de debit sont appliqué à chacun des cubes. 


_* Note : J'ai signalé ce bug de màj d'affichage au support de QIDI mais à ce jour aucun correctif ..._

Laisser les cubes refroidir sur le plateau le temps qu'ils reviennent à temperature ambiante cela limitera le risque de déformation.


Proceder a une inspection visuelle des cubes imprimés pour s'assurer qu'ils sont correctements imprimés et conformes.


### Mesure des Parois des Cubes

Mesurer avec precision les parois X1, X2, Y1 et Y2 de chacuns des cubes à l'aide d'un micrometre precision 1/100.





Télécharger le fichier tableur [17_10_2024_Calibration_filament_Débit_Ecoulement.ods](https://github.com/sudtek/IMPRIMANTES_3D/blob/e164b41cd4a32ed06201bcb55994184bbe3e5474/QIDI/IFAST/CALIBRATION/Etape%2004/17_10_2024_Calibration_filament_D%C3%A9bit_E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)

Dupliquer l'onglet **PROFORMAT_Debit_Filament_Matrice_Cubes_10C_x_1L_Y%..Z%_Pas_N%** pour y saisir les valeurs des parois X1,X2,Y1,Y2 de chacun de vos cubes.



### Analyse des Données

Le tableur calculera les valeurs moyennes arithmétiques (x1+x2+y1+y2)/4 de chaque cube et dessinera automatiquement un graphe composé d'une polyligne. Ce graphe a pour but de vous aider à localiser un intervale solution ou vous pourrez trouver à minima une solution. Un intervale solution c'est une ligne entre deux points Mmoy et Nmoy qui coupe pour une valeur d'épaisseur 1,6mm. Cette valeur correspond à lépaisseur d'une coque * nombre de coques qui compose une paroi (0,4mm*4=1,6mm). Dans le fichier tableur vous trouverez un onglet intitulé :"Exemple_Test_Debit_Filament_Matrice_Cubes_10C_x_1L_100%..90%_Pas_1%" qui correspond à une serie que j'ai effectuée suite à la caractérisation d'une de mes bobines de PETG qui me servira de référence pour la suite de mes explications. 



_Note : Si vous ne trouvez pas d'intervale solution compris dans l'intervale inital [100% .. 90%]% de débit il doit se situer à proximité immédiate de la borne inférieure ou supérieure, si ce n'est pas le cas il y a fort à parier que vous avez mal caractérisé le diamétre principal de votre filament reportez-vous à l'[Étape 03 : Calibration du diamètre du filament](https://github.com/sudtek/IMPRIMANTES_3D/blob/8ec18aae8171912256d8da4de497ad06e5ea1aaa/QIDI/IFAST/CALIBRATION/Etape%2003/Etape_03.md) et reprendre ce tuto depuis le début._

Cette polyligne composée de segments coupe pour une valeur d'épaisseur 1,6mm entre les cubes de débit de 92.0% et 91.0%; il y a bien une solution dans cet intervale sachant que graphiquement on constate que ces deux bornes ne sont pas solutions. Le % débit solution est donc compris dans l'intervale ]92% .. 91%[ (entre le cube 92% et le cube 91% exclus). Sachant que la précision de saisi dans le sliccer IDEAMAKER pour le % de débit est 1/10 (0.1)

Vous pouvez au choix :

- Vous arreter ici et "couper la poire en deux" en choisisant une valeur intermédiare; en observant soigneusement le graphique on comprend intuitivement que la solution est située dans le demi intervale de gauche compris entre ]92% .. 91.5%[ soit au choix {91.6%;91.7%;91.8%} avec une erreur de maximum de +- 0.2% c'est trois points sont acceptable.

- Rechercher la valeur exacte à 0,1% ce qui implique d'imprimer une nouvelle série de cubes de débit dans l'intervale [92.0% 91.0%]

### Détermination du Débit Optimal
Avant de réaliser ce tutoriel, j'avais opté pour une méthode de dichotomie pure, consistant à effectuer plusieurs séries de deux cubes, représentant les bornes supérieure et inférieure d'un intervalle. Cependant, cette méthode nécessite l'impression récursive d'environ six séries de cubes pour converger et déterminer la valeur du débit à 0,1 % près. Cette approche est chronophage et fastidieuse, car il faut laisser chaque série de cubes revenir à température ambiante avant de procéder aux mesures, et il est crucial de ne pas se tromper dans la mise en œuvre de la dichotomie (choix de l'intervalle).

Le seul avantage de cette solution est qu'elle met en évidence l'existence de plusieurs candidats solutions dans l'intervalle global pour le pourcentage de débit, certains étant de meilleurs candidats que d'autres en raison du phénomène de dispersion/regroupement autour de la valeur consigne de 1,6 mm. Ainsi, pour un même filament, j'ai pu trouver deux bons candidats : 91,7 % et 92,3 %.

Pour les plus curieux, reportez-vous à cette vidéo qui reprend tout le modus operandi de la recherche du pourcentage de débit pour l'intervalle de 100 % à 90 %, présentée ci-dessus  Détail, explications et méthode de calibration du % de débit avec une série de 11 cubes de calibration 100% à 90% (https://www.youtube.com/watch?v=gn3A1lFX0vc?si=RjfHDFoegoFpW7tH)
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

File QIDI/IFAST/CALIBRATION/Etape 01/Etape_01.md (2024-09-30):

**Étape 01 : Calibration des deux moteurs d'extrusion de Z1 et Z2**

Prérequis avant de continuer : Vous devez avoir validé [l'étape 00 Réglage de l'alignement des deux buses / calibrage XY](https://github.com/sudtek/IMPRIMANTES_3D/blob/main/QIDI/IFAST/CALIBRATION/Etape%2000/Etape_00.md)

### Présentation

Cette étape consiste à vérifier si les extrudeurs de la QIDI I-Fast consomment une longueur précise de filament conforme à la consigne du G-code, généralement 100 mm. Cette vérification nécessite au minimum un pied à coulisse ou une règle métallique de précision.

Si, en exécutant le G-code, chacun de vos extrudeurs consomme exactement 100 mm de filament, vous avez de la chance et n'avez rien à calibrer. Vous pouvez passer à l'étape suivante [Calibration Mise à niveau du plateau ](https://github.com/sudtek/IMPRIMANTES_3D/blob/main/QIDI/IFAST/CALIBRATION/Etape%2002/Etape_02.md).

Dans le cas contraire, si un ou les deux extrudeurs présentent une sur-extrusion ou une sous-extrusion, vous devrez calculer et définir les pas/mm pour chacun des moteurs extrudeurs E. Les cas de sur-extrusion et de sous-extrusion sont définis comme suit :
- **Sur-extrusion** : Extrusion de 111 mm de filament pour une consigne initiale de 100 mm -> vous avez consommé plus de filament que prévu.
- **Sous-extrusion** : Extrusion de 97 mm de filament pour une consigne initiale de 100 mm -> vous avez consommé moins de filament que prévu.

Cette procédure doit impérativement être effectuée chaque fois que vous remplacez ou changez la tête de votre QIDI I-Fast. Si vous conservez toujours la même tête, sauf en cas d'usure excessive ou d'autres problèmes, ces réglages ne devraient normalement pas changer dans le temps. En cas de doute, vous pouvez à tout moment revérifier en chargeant le G-code de calibration adapté avec des valeurs de températures adaptées en fonction de la matière de vos filaments.

Par principe, on peut calibrer les pas des moteurs d'extrudeurs avec n'importe quel type de filament, peu importe la matière PLA, PETG...

Dans mon cas, j'utilise du PETG sur la tête de gauche nommée Z2 et du PLA sur la tête Z1. Le PETG me sert pour imprimer les corps de pièces, le PLA lui est utilisé pour les supports, ce qui facilite le retrait des supports après impression.

### Important

Mon choix d'affecter le PETG à Z2 et le PLA à Z1 n'est pas arbitraire : Cette décision est "imposée" par mon slicer IdeaMaker, qui utilise une convention de référencement des têtes/buses particulière. Par conséquent, le profil de filament dominant pour imprimer un corps de pièce est la tête la plus à gauche dans IdeaMaker, ce qui correspond à Z2. Si vous n'utilisez pas IdeaMaker et que vous utilisez le logiciel slicer de QIDI (ou un autre), il se peut que vous ne soyez pas concerné par ce cas. Cependant, je ne peux pas en être certain puisque je n'utilise pas d'autres logiciels de slicing. Il vous incombe donc de vérifier et d'adapter le G-code en fonction de vos besoins.

Note : Si plus tard vous envisagez d'utiliser IdeaMaker, je vous recommande d'adopter les mêmes choix que moi ainsi vous pourrez directement utiliser mes profils IdeaMakers.

Récapitulatif des paramètres pour la procédure de calibration des moteurs pas à pas des extrudeurs de ma QIDI IFAST :

```markdown
| Extrudeur situé à main | Gauche | Droite |
|------------------------|--------|--------|
| Référence QIDI I-Fast  | Z2     | Z1     |
| Matière                | PETG   | PLA    |
| Température buse       | 235°C  | 205°C  |
| Couleur filament       | Blanc  | Mauve  |
| Débit d'écoulement     | 100%   | 100%   |
| Longueur de calibrage  | 100 mm | 100 mm |
```

Mon fichier gcode de calibrage [03_09_2024_RAZ_extrude_100mm.gcode](https://github.com/sudtek/IMPRIMANTES_3D/blob/572e1f38047cff27d3ebf05762a64709f86ebc43/QIDI/IFAST/CALIBRATION/Etape%2001/gcode/03_09_2024_RAZ_extrude_100mm.gcode) se chargera d'extruder le filament les deux têtes de 100 mm l'une après l'autre et à aux température adéquates pour du PETG et du PLA.

Si vous voulez calibrer votre imprimante avec d'autres filaments et ou combinaisons (PLA/PLA, PETG/ABS ...),** il faudra télécharger le fichier gcode et l'adapter à votre situation des température attendues par la matière que vous avez choisi d'extruder**. Exemple de modification du gcode de mon programme pour avoir du PLA sur Z1 et Z2 à 205°C :

```gcode
; ----------------------------------------------------
; Fixer la température des deux buses

; Buse de gauche Z2 alias T1 pour du PLA à 205°C
M109 T1 S205

; Buse de droite Z1 alias T0 pour du PLA à 205°C
M109 T0 S205

; Note : M109 attend que la température de consigne soit atteinte avant de continuer -> ne pas remplacer par M104
; ----------------------------------------------------
```

Note : Pour cette opération, le plateau doit rester en bas, il est donc inutile de le faire chauffer, idem pour l'enceinte !

P1) Charger deux bobines bien sèches et désydratées, prévoir 24 heures de désydratation, dans mon cas bobine de gauche type PETG blanc, bobine de droite type PLA mauve.

P2) Ne pas installer les tubes de guidage PTFE bleu, au besoin les retirer car ils vous empêcheront de marquer et mesurer les longueurs de filaments.

P3) Via le menu de la QIDI IFAST, déplacer la tête au centre du plateau XY, (ATTENTION ne jamais déplacer la tête à la main).

P4) À l'aide d'un réglé ou d'un pied à coulisse, mesurer précisément 100 mm sur chacun des filaments et dessiner une trace précise avec un feutre, soyez le plus précis possible, cela aura de l'influence. Réaliser une seconde trace à 200 mm de la tête. ATTENTION lorsque vous prendrez appui avec le réglé / pied à coulisse et qui risque de faire varier la mesure de quelques millimètres... Ces millimètres sont cruciaux donc faites attention et soyez le plus précis possible !

P5) Fixer manuellement la température de préchauffage des filaments, dans mon cas Z2 à 235°C et Z1 à 205°C. Bien que mon programme se charge de fixer ces valeurs et d'attendre qu'elles soient atteintes avant d'enchaîner, cette habitude vous évitera un jour d'extruder par erreur à trop basse température et détériorer une tête...

P6) Exécuter le gcode [03_09_2024_RAZ_extrude_100mm.gcode](https://github.com/sudtek/IMPRIMANTES_3D/blob/572e1f38047cff27d3ebf05762a64709f86ebc43/QIDI/IFAST/CALIBRATION/Etape%2001/gcode/03_09_2024_RAZ_extrude_100mm.gcode) . Z2 et Z1 vont monter en température et extruder tour à tour une longueur proche de 100 mm.

P7) Mesurer la distance entre le 0 de référence (le collier non enfoncé) de la tête et le 1er trait pour Z2, idem pour Z1.

**// Note : Ajouter une photo !**
Simplon.co

Exemple de tests réalisés sur ma IFAST avec débit 100% pour 100 mm :

- Gauche Z2 PETG 235°C et en sous-extrusion il reste +4 mm de filament.
- Droite Z1 PLA 205°C et en sous-extrusion il reste +6.2 mm de filament.

S'il reste quelques mm entre le colier et le trait mais que vous n'arrivez pas à mesurer voici l'astuce : Mesurer la distance entre le 0 de référence (le collier non enfoncé) de la tête et le second trait pour par exemple Z2 (idem pour Z1).
Exemple :

- Extrudeur de gauche Z2 PETG 235°C sous-extrusion la longueur de filament restante jusqu'au second trait est de +101.5 mm soit (200-101.5) = +98.5 mm  ... cela vous evitera de galérer et vous contortionner ;)  
  
P8) Appliquer la formule suivante pour calculer les nouveaux E de Z2 et Z1 :
- Extrudeur de gauche Z2 PETG 235°C sous-extrusion reste de +4 mm -> (200-104)=96mm -> 96*0.0073/100 = 0.0070
- Extrudeur de droite Z1 PLA 205°C sous-extrusion reste de +6.2 mm -> (200-106.2)= 93.8mm -> 93.8*0.0073/100 = 0.0068

### Le cas particulier de la sur-extrusion :

Si le 1er trait à 100mm est sous le colier le plus simple est de réinitialiser aux valueurs d'orrigines et vous vous retrouverez à nouveau en sous extrusion. 

```gcode
; QIDI IFAST : T0 = buse de droite = Z1 = S
; QIDI IFAST : T1 = buse de gauche = Z2 = P

M8011 S0.0073 P0.0073
```
Télécharger le fichier [09_09_2024_RESTORE_DEFAUT_E_Z1Z2.gcode](https://github.com/sudtek/IMPRIMANTES_3D/blob/572e1f38047cff27d3ebf05762a64709f86ebc43/QIDI/IFAST/CALIBRATION/Etape%2001/gcode/09_09_2024_RESTORE_DEFAUT_E_Z1Z2.gcode)

Lancer l'impression du gcode, faites un reboot de l'imprimante et reprendre à la phase P04).

-----------------

### Sauvegarder la nouvelle valeur dans le firmware de la QUIDI IFAST :

Pour remplacer et sauvegarder les nouvelles valeurs afin de définir les nouveaux pas/mm pour E correspondant à votre Z1 et Z2 il sufit de copier le bout de code suivant et remplacer par vos valeurs, le sauvegarder sous un nom de fichier explicite exemple "JJ_MM_AAAA_SAVNEW_Pas_E_Z1Z2.gcode" et l'executer en l'imprimant sur la QIDI IFAST, cela prendra 1 seconde. 

```gcode
; QIDI IFAST : T0 = buse de droite = Z1 = S
; QIDI IFAST : T1 = buse de gauche = Z2 = P

M8011 S0.0068 P0.0070
```
Télécharger le fichier [09_09_2024_SAV_NEW_E_Z1Z2.gcode](https://github.com/sudtek/IMPRIMANTES_3D/blob/572e1f38047cff27d3ebf05762a64709f86ebc43/QIDI/IFAST/CALIBRATION/Etape%2001/gcode/09_09_2024_SAV_NEW_E_Z1Z2.gcode)

-----------------

### Vérification de la bonne prise en compte des nouvelle valeur du firmware de la QUIDI IFAST :

Aprés mise à jour, 

- Redémarez / rebootez votre IFAST.

- Vérifiez que les nouvelles valeurs de S & P permette l'extrusion conforme de de 100mm sur les des deux buses. [09_09_2024_VERIF_Z1Z2_extruder_100mm.gcode](https://github.com/sudtek/IMPRIMANTES_3D/blob/572e1f38047cff27d3ebf05762a64709f86ebc43/QIDI/IFAST/CALIBRATION/Etape%2001/gcode/09_09_2024_VERIF_Z1Z2_extruder_100mm.g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)
- Si aprées extrusion le 1er trait 100mm est bien au niveau du collier l'extrusion de votre machine est parfaitement calibrée pour les deux buses et avez totalement validé cette étape.

-----------------

Tous les gcodes de calibration de E sont disponibles: [Ici](https://github.com/sudtek/IMPRIMANTES_3D/blob/572e1f38047cff27d3ebf05762a64709f86ebc43/QIDI/IFAST/CALIBRATION/Etape%2001/gcode)

_Note #1 Important pour les utilisateurs Ideamaker, dans le profil de l'imprimante Ideamaker intégre une variable nommée: **step E / mm = 0.00** ; par defaut elle vaut 0.00 si vous changez cette valeur alors Ideamaker ne tiendra pas compte de notre calibrage et appliquera la valeur au deux moteurs d'extrusion ... donc assurez-vous que dans le profil imprimante Ideamaker votre variable nommée vaut 0.00 ! **step E / mm = 0.00**_. Cette variable est un option acceptable si et seulement si vous avez un seul moteur d'extrusion E !

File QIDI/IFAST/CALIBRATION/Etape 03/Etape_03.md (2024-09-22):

# Étape 03 : Calibration du diamètre du filament

## Prérequis avant de continuer
- Ce tutoriel doit être effectué avec des bobines qui sont parfaitements désidratées.
- Un appareil de mesure de précision type pied à coulisse ou un palper et nécessaire pour correctement mesurer le diamétre, vous reporter à la section [A propos des instruments de
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

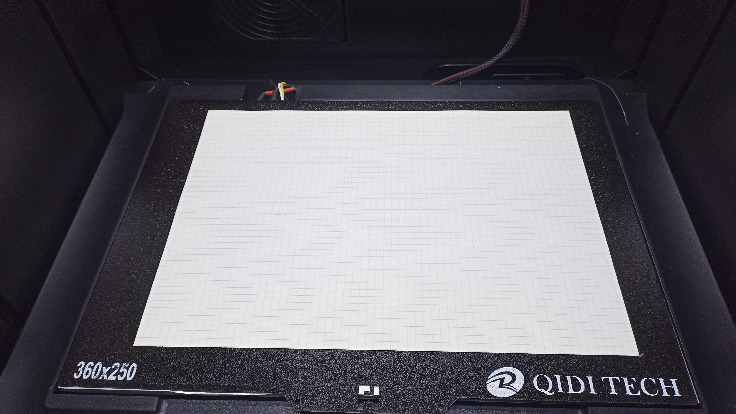
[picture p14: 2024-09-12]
QIDI/IFAST/CALIBRATION/Etape 02/media/Feuille_A4_Bristol_0,02mm.jpg

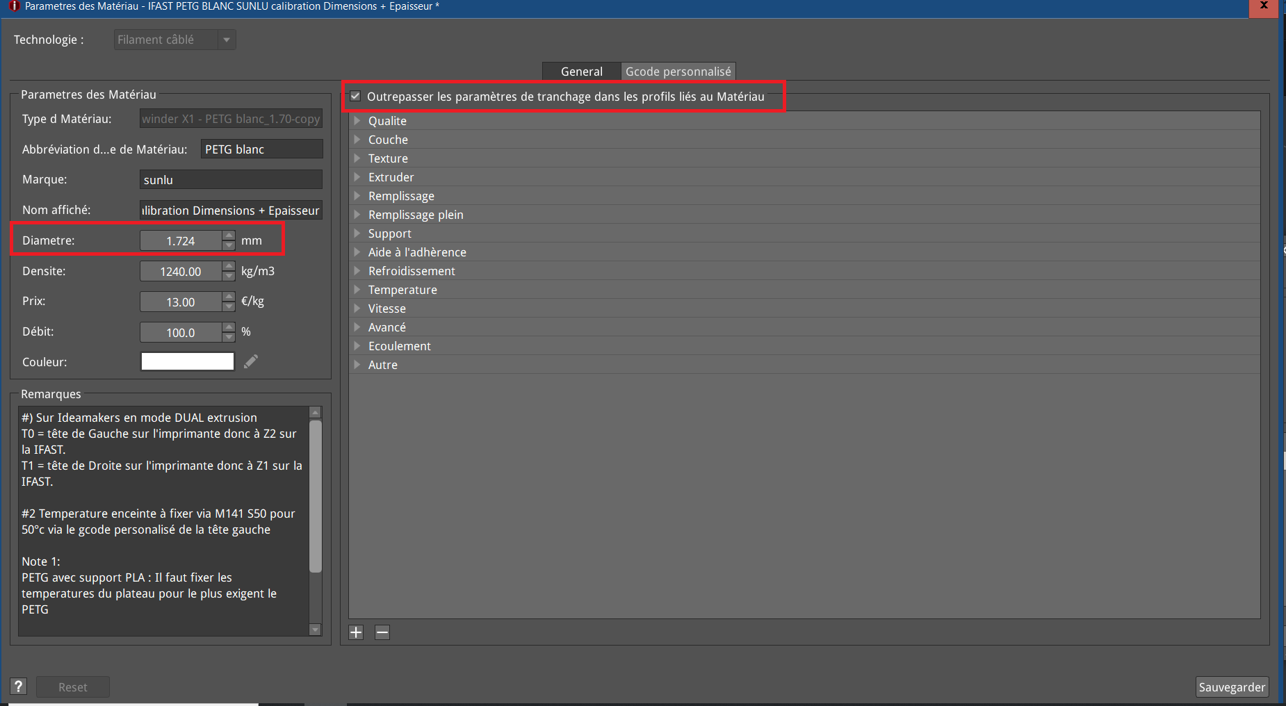
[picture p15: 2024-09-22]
QIDI/IFAST/CALIBRATION/Etape 03/media/IDEAMAKER_Fixer_Diametre_moyen_filament.png

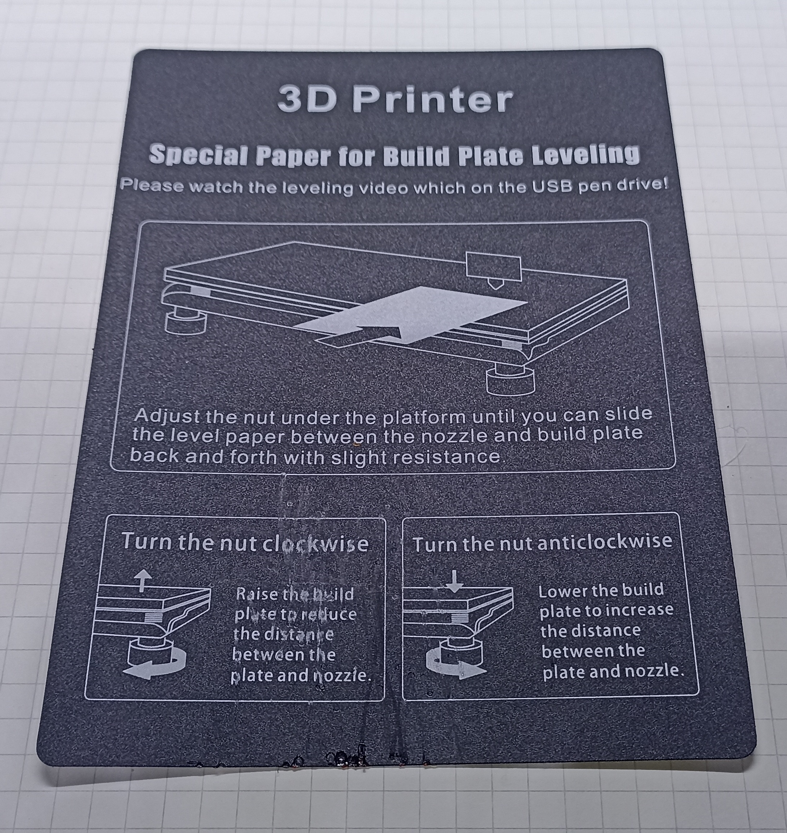
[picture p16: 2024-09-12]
QIDI/IFAST/CALIBRATION/Etape 02/media/Gauge_plastique_livrée_par_QIDI.jpg

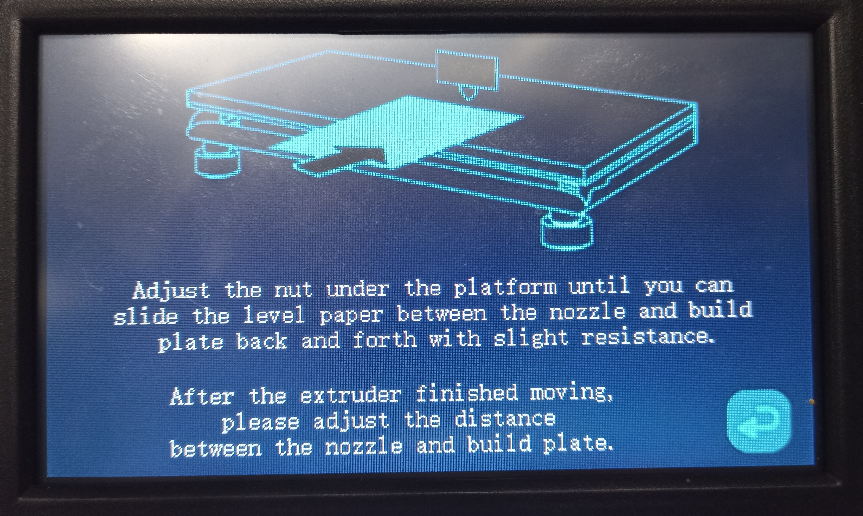
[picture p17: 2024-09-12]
QIDI/IFAST/CALIBRATION/Etape 02/media/Menu_Ajustement_normal_levelling.jpg

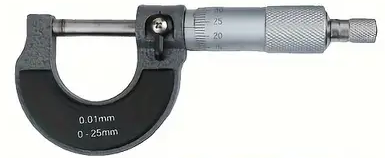
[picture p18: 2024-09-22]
QIDI/IFAST/CALIBRATION/Etape 03/media/palper.png

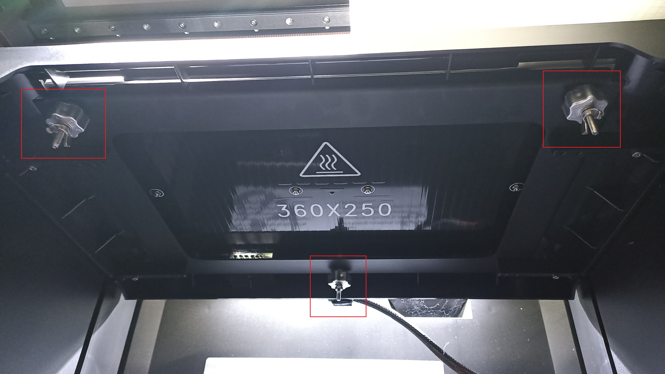
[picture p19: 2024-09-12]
QIDI/IFAST/CALIBRATION/Etape 02/media/Les_3_noix.jpg

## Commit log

2024-08-24 Update Roadmap calibration.txt
2024-08-24 Update 23_08_2024 Calibrage 2 extruders 100mm T1_G_Z2_PETG_235 & T0_D_Z1_PLA_205 OK.gcode
2024-08-25 Update and rename Roadmap calibration.txt to Roadmap calibration.md
2024-08-26 Update Roadmap calibration.md
2024-08-26 Create Adaptateurs de bobines tierces.md
2024-08-26 Update Adaptateurs de bobines tierces.md
2024-09-03 Update and rename 23_08_2024 Calibrage 2 extruders 100mm T1_G_Z2_PETG_235 & T0_D_Z1_PLA_205 OK.gcode to 23_08_2024_calibrage_ extruders_100mm_T1_G_Z2_PETG_235_T0_D_Z1_PLA_205_OK.gcode
2024-09-09 Update and rename QIDI/IFAST/QIDI IFAST Firmware V3.4/[Qidi-Fast] V3.40-厂里参数.gcode to QIDI/IFAST/Firmware /V3.4/[Qidi-Fast] V3.40-厂里参数.gcode
2024-09-09 Update and rename QIDI/IFAST/Firmware /V3.4/[Qidi-Fast] V3.40-厂里参数.gcode to QIDI/IFAST/Firmware /[Qidi-Fast] V3.40-厂里参数.gcode
2024-09-09 Update and rename [Qidi-Fast] V3.40-厂里参数.gcode to [Qidi-Fast] V3.40-厂里参数.gcode
2024-09-21 Rename QIDI/IFAST/CALIBRATION/Etape 03/ee.txt to QIDI/IFAST/CALIBRATION/Etape 03/QIDI/IFAST/CALIBRATION/Etape 03/Etape_3.md
2024-09-21 Rename QIDI/IFAST/CALIBRATION/Etape 03/QIDI/IFAST/CALIBRATION/Etape 03/Etape_03.md to QIDI/IFAST/CALIBRATION/Etape 03/Etape_03.md
2024-11-05 Rename Calibration [100%..90%].zip to 05_11_2024_IDEAMAKER_Calibration.zip
2024-11-05 Rename QIDI/IFAST/CALIBRATION/Etape 04/IDEAMAKER_menu_tranchage_Ligne4_TEMPLATEMATERIAUX.png to QIDI/IFAST/CALIBRATION/Etape 04/media/IDEAMAKER_menu_tranchage_Ligne4_TEMPLATEMATERIAUX.png
2024-11-05 Rename QIDI/IFAST/CALIBRATION/Etape 04/IDEAMAKER_menu_tranchage_Ligne1_IMPRIMANTE.png to QIDI/IFAST/CALIBRATION/Etape 04/media/IDEAMAKER_menu_tranchage_Ligne1_IMPRIMANTE.png
2024-11-05 Rename QIDI/IFAST/CALIBRATION/Etape 04/IDEAMAKER_menu_tranchage_Ligne2_PETG.png to QIDI/IFAST/CALIBRATION/Etape 04/media/IDEAMAKER_menu_tranchage_Ligne2_PETG.png
2024-11-05 Rename QIDI/IFAST/CALIBRATION/Etape 04/IDEAMAKER_menu_tranchage_Ligne3_PLA.png to QIDI/IFAST/CALIBRATION/Etape 04/media/IDEAMAKER_menu_tranchage_Ligne3_PLA.png
